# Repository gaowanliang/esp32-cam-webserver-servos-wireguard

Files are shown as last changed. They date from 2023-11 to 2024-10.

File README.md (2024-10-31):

# ESP32-CAM example revisited - Supports dual-degree-of-freedom servos and wireguard-based intranet penetration &nbsp;&nbsp;&nbsp; 
<span title="Master branch build status">

</span> &nbsp;&nbsp;
<span title="ESP EYE">ESP-EYE logo</span>

## Taken from the ESP examples, and expanded
> [!IMPORTANT]
> Since this code is old, it does not support esp32 version 3.x. Please use esp32 version 2.0.17 to compile it.
> 由于此代码较为老旧，所以不支持 esp32 3.x 版本，请使用esp32 2.0.17 版本编译

支持双自由度舵机和基于Wireuard的内网穿透

### Intranet Penetration Modifications

Configure your own wireguard parameters in myconfig.h

```c
// WireGuard settings
IPAddress local_ip(10, 0, 0, 2);                                            // IP address of the local interface
const char private_key[] = "oKXeV7gGtYTVcdgNKciDTkTLvmlZLbrzEcwpbXUDZH8=";  // Private key of the local interface
const char endpoint_address[] = "1.1.1.1";                           // Address of the endpoint peer
const char public_key[] = "0UWkW7oYVivNxoUX6OZWvhlpXcOeiX1FK682xNNDPxA=";   // Public key of the endpoint peer
uint16_t endpoint_port = 51280;                                             // Port of the endpoint peer
```

Your server can refer to the following configuration

```ini
[Interface]
Address = 10.0.0.1/24
ListenPort = 51280
PrivateKey = 8OZckuFQTgTczXnE0nJosrqVkxdi/GKS2fwmYOK53WA=

[Peer]
PublicKey = zV4LrlkKV7ne4zruqTgWfg6U4v7qL89YT2Q3I+5E7Gw=
AllowedIPs = 10.0.0.2/32
```
Please note, please do not use the above parameters directly, direct use may bring a series of security problems, you can use [this page](https://wg.orz.tools/) to generate your own `public key` and `private key`.

#### Refer

https://github.com/andr13/ESP32-Web-WireGuard

https://github.com/askew-etc/esp32-cam-webserver-servos

### Servo Modifications

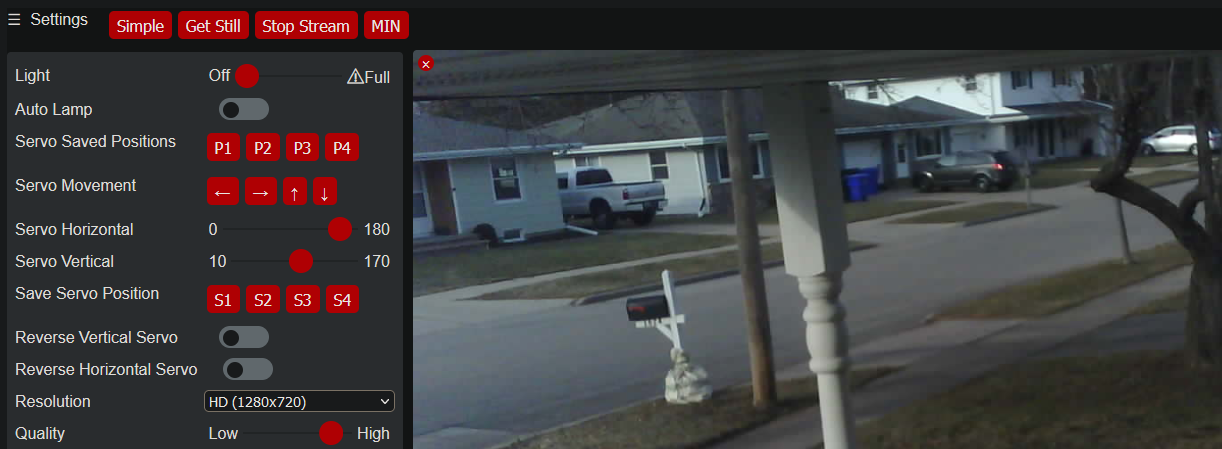
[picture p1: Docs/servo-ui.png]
Servo UI Screenshot


> [!NOTE]
> I'm in the process of redesigning this case, the current one may be too compact, while there are safety issues with not reserving a place for the charging port to be secured.

3D Printer files for tilt and pan with covers: https://www.thingiverse.com/thing:4621865.
You can buy the tilt and pan hardware with the screws along with the two servos from places like [Amazon](https://www.amazon.com/dp/B0775R6JFF) or [AliExpress](https://www.aliexpress.us/item/3256804363840656.html). Then you just need to 3D print Front_Cover.stl, Bottom_Cover.stl, and Mount_Original.stl.
I did exactly that, however the clips didn't quite catch on the two rectangular insets on the sides of Mount_Original.stl, so I used Blender to make them slightly bigger so that the clip could actually catch in them. Probably don't need to do that if printing all the pieces yourself since I assume they would just fit correcty. I've included these three files, two of which I modified to fit better. The front cover I modified as well since it fits a tad too tight with the back cover.
The pan and tilt [hardware](https://www.aliexpress.us/item/3256804363840656.html) and [servos](https://www.amazon.com/dp/B07Q6JGWNV) can be bought separately, useful if doing a bunch, or just utilizing one servo for panning only.

The servos use GPIO pins 12 and 13, making it easy to just use a four-pin female header to plug into the ESP-32, and then create the connections for input ground and power as well as the ground, power, and data lines of the servos.

In many applications the tilting feature is probably unnecessary and can be omitted to cut down on hardware.

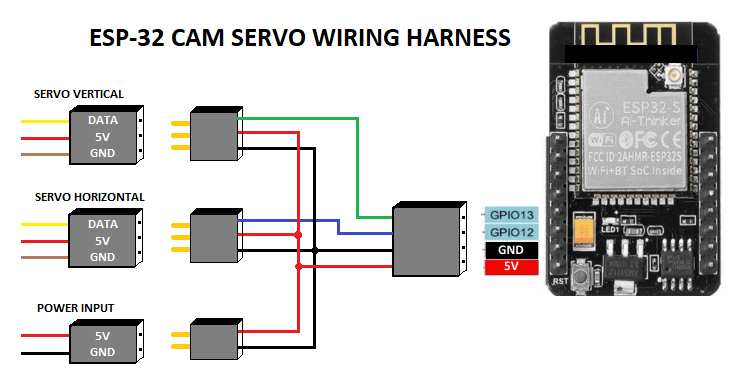
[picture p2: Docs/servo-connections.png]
Servo Wiring Harness


### Original Documentation

This sketch is a extension/expansion/rework of the 'official' ESP32 Camera example sketch from Espressif:

https://github.com/espressif/arduino-esp32/tree/master/libraries/ESP32/examples/Camera/CameraWebServer

But expanded with:
* Servo control (horizontal and vertical)
* More options for default network and camera settings
* Save and restore settings
* Control of on-board lamps, rotate the view in the browser
* Dedicated standalone stream viewer
* Over The Air firmware updates
* Lots of minor fixes and tweaks, documentation etc.

And 'reduced' by removing the Face Recognition features
* **If you want to try the Face Recognition features** please use the [`3.x` maintenance branch](https://github.com/easytarget/esp32-cam-webserver/tree/3.x), which still recieves bugfixes, but is not receiving any further development.
* They were a demo, only worked in low resolution modes, did not preserve the face database between power cycles, and were of little use in real-world applications.
* There are other (specialised) sketches for the ESP-CAM that do use face recognitioni more effectively, if this is your thing :-)

The original example is a bit incomprehensible and hard to modify as supplied. It is very focused on showing off the face recognition capabilities, and forgets the 'webcam' part.
* There are many other variants of a webcam server for these modules online, but most are created for a specific scenario and not good for general, casual, webcam use.

Actually, there are two cats in this image!

Hopefully this expanded example is more useful for those users who wish to set up a simple ESP32 based webcam using the cheap(ish) modules freely available online. Especially the AI-THINKER board:

#### AI-THINKER ESP32-CAM vs Other Modules:

I have four [AI-THINKER ESP32-CAM](https://github.com/raphaelbs/esp32-cam-ai-thinker/blob/master/assets/ESP32-CAM_Product_Specification.pdf) boards, so the descriptions below are for that board. But I took care to leave the default definitions and controls for other boards in the example intact. You may need to adjust the programming method to suit the your board, look for examples online.

* For some other good examples and information on ESP32 based webcams I also recommend the sketches here:
https://github.com/raphaelbs/esp32-cam-ai-thinker
* The AI thinker wiki can be quite informative, when run through an online translator and read sensibly:
https://wiki.ai-thinker.com/esp32-cam
* Default pinouts are also included for WRover Kit, ESP Eye and M5Stack esp32 camera modules.
  I do not have any of these boards, so they are untested by me. Please [let me know](https://github.com/easytarget/esp32-cam-webserver/issues) if you find issues or have a board not [in the list](./camera_pins.h).

## Troubleshooting:

A lot of common issues with this sketch are discussed and covered in the discussion forums:

https://github.com/easytarget/esp32-cam-webserver/discussions/categories/common-issues

The existing [issues list](https://github.com/easytarget/esp32-cam-webserver/issues?q=is%3Aissue) on Github is a good place to start if you have a specific issue not covered above or in the forums.

There is also this excellent guide for help with some common issues seen with the camera modules:
https://randomnerdtutorials.com/esp32-cam-troubleshooting-guide/

### Known Issues

Builds made with PlatformIO are currently (v4.0) broken; the stream will die shortly after starting. See https://github.com/easytarget/esp32-cam-webserver/issues/218 for more info.

The ESP32 itself is susceptible to the usual list of WiFi problems, not helped by having small antennas, older designs, congested airwaves and demanding users. The majority of disconnects, stutters and other comms problems are simply due to 'WiFi issues'. The AI-THINKER camera module & esp32 combination is quite susceptible to power supply problems affecting both WiFi conctivity and Video quality; short cabling and decent power supplies are your friend here; also well cooled cases and, if you have the time, decoupling capacitors on the power lines.

A basic limitation of the sketch is that it can can only support one stream at a time. If you try to connect to a cam that is already streaming (or attempting to stream) you will get no response and, eventually, a timeout. The stream itself is a [MJPEG stream](https://en.wikipedia.org/wiki/Motion_JPEG), which relies on the client (the web browser) to hold the connection open and request each new frame in turn via javascript. This can cause errors when browsers run into Javascript or caching problem, fail to request new frames or refuse to close the connection.
* If you cannot start the stream you can check the `/dump` page of the cam to see if it currently reports the camera as streaming or not.

Note that I do not respond to any Private Messages (via github, hackaday, or wherever) for support.

## Setup:

* For programming you will need a suitable development environment, I use the Arduino IDE, but this code should work in the Espressif development environment too.
* Make sure you are using the [latest version](https://www.arduino.cc/en/main/software#download) of the IDE and then follow [This Guide](https://docs.espressif.com/projects/arduino-esp32/en/latest/installing.html) to set up the Espressif Arduino core for the IDE.
* _I do not recommend or support running with development builds of either the IDE or the ESP arduino core._
* If you have a development board (anything that can be programmed via a standard USB cable/jack on the board itself) you are in luck. Just plug it in and skip ahead to the [config](#config) section. Remember to set your board model.
* The AI-THINKER board requires use of an external **3.3v** serial adapter to program; I use a `FTDI Friend` adapter, for more about this read AdaFruits excellent [FTDI Friend guide](https://learn.adafruit.com/ftdi-friend).
* Be careful not to use a 5v serial adapter since this will damage the ESP32.

### Wiring for AI-THINKER Boards (and similar clone-alikes)

Is pretty simple, You just need jumper wires, no soldering really required, see the diagram below.
Hoockup
* Connect the **RX** line from the serial adapter to the **TX** pin on ESP32
* The adapters **TX** line goes to the ESP32 **RX** pin
* The **GPIO0** pin of the ESP32 must be held LOW (to ground) when the unit is powered up to allow it to enter it's programming mode. This can be done with simple jumper cable connected at poweron, fitting a switch for this is useful if you will be reprogramming a lot.
* You must supply 5v to the ESP32 in order to power it during programming, the FTDI board can supply this.

### Download the Sketch, Unpack and Rename
Download the latest release of the sketch from https://github.com/easytarget/esp32-cam-webserver/releases/latest
- You can get the latest stable development release by cloning / downloading the `master` branch of the repo.

This will give you an archive file with the Version number in it, eg.`esp32-cam-webserver-4.0.zip`. You need to unpack this into your Arduino sketch folder, and then you need to **rename the folder you extracted to remove the version number**, eg.`esp32-cam-webserver-4.0` becomes `esp32-cam-webserver`.

Once you have done that you can open the sketch in the IDE by going to the `esp32-cam-webserver` sketch folder and selecting `esp32-cam-webserver.ino`.

### Config

By default the sketch assumes you have an AI-THINKER board, it creates an AccessPoint called `ESP32-CAM-CONNECT` and with the password `InsecurePassword`; connect to that and then browse to [`http://192.168.4.1/`](http://192.168.4.1/). This is nice and easy for testing and demo purposes.

To make a permanent config with your home wifi settings, different defaults or a different board; copy (or rename) the file `myconfig.sample.h` in the sketch folder to `myconfig.h` and edit that, all the usable defaults are in that file. Because this is your private copy of the config it will not get overwritten if you update the main sketch!

### Programming

Assuming you are using the latest Espressif Arduino core the `ESP32 Dev Module` board will appear in the ESP32 Arduino section of the boards list. Select this (do not use the `AI-THINKER` entry listed in the boiards menu, it is not OTA compatible, and will caus the module to crash and reboot rather than updating if you use it.
IDE board config

Make sure you select the `Minimal SPIFFS (1.9MB APP with OTA/190KB SPIFFS)` partition scheme and turn `PSRAM` on.

The first time you program (or if OTA is failing) you need to compile and upload the code from the IDE, and when the `Connecting...` appears in the console reboot the ESP32 module while keeping **GPIO0** grounded. You can release GPO0 once the sketch is uploading, most boards have a 'boot' button to trigger a reboot.

Once the upload completes (be patient, it can be a bit slow) open the serial monitor in the IDE and reboot the board again without GPIO0 grounded. In the serial monitor you should see the board start, connect to the wifi and then report the IP address it has been assigned.

Once you have the initial upload done and the board is connected to the wifi network you should see it appearing in the `network ports` list of the IDE, and you can upload wirelessly.

If you have a status LED configured it will give a double flash when it begins attempting to conenct to WiFi, and five short flashes once it has succeeded. It will also flash briefly when you access the camera to change settings.

Go to the URL given in the serial output, the web UI should appear with the settings panel open. Click away!

## My Modifications:

The simplified viewer<br>*The new default Simple view, just the basics*

The WiFi details can be stored in an (optional) header file to allow easier code development, and a camera name for the UI title can be configured. The lamp and status LED's are optional, and the lamp uses a exponential scale for brightness so that the control has some finess.

All of the face recognition code has been removed as of V4.0; this reduces the code size enough to allow OTA programming while improving compile and programming times.

The compressed and binary encoded HTML used in the example has been unpacked to raw text, this makes it much easier to access and modify the Javascript and UI elements. Given the relatively small size of the index page there is very little benefit from compressing it.

The streamviewer, lamp control, and all the other new features have been added. I have tried to retain the basic structure of the original example,extending where necessary.

The web UI has had changes to add the lamp control (only when enabled) and make the streamm window rotate and resize appropriately. I also made the 'Start Stream' and 'Snapshot' controls more prominent, and added feedback of the camera name + firmware.

I would also like to shoutout to @jmfloyd; who suggested rotating the image in the browser since the esp32 itself cannot do this.

The stream viewer<br>*Standalone StreamViewer; No decoration or controls, the image is resizable, and you can doubleclick it for fullscreen*

The info page<br>*Boring Details, useful when debugging or if you want to check stats*

### API
The communications between the web browser and the camera module can also be used to send commands directly to the camera (eg to automate it, etc) and form, in effect, an API for the camera.
* I have [documented this here](https://github.com/easytarget/esp32-cam-webserver/blob/master/API.md).

## Notes:

* I only have AI-THINKER modules with OV2640 camera installed; so I have only been able to test with this combination. I have attempted to preserve all the code for other boards and the OV3660 module, and I have merged all changes for the WebUI etc, but I cannot guarantee operation for these.
* I created a small board with a handy switch for power, a pushbutton for the GPIO0 programming switch, and a socket for the AI-THINKER board. This proved very useful for development work and programming multiple devices.
* I found some excellent [cases on Thingieverse](https://www.thingiverse.com/thing:3708345).

Cameras and a Programmer

## Contributing

Contributions are welcome; please see the [Contribution guidelines](CONTRIBUTING.md).

## Plans

Time allowing; my Current plan is:

V4
* Investigate using SD card to capture images
* Implement a better network stack for remembering multiple AP's, auto-config etc.
  * Advanced (web upload) OTA might be nice to have if possible
* UI Skinning/Theming
* OSD
  * Temperature/humidity/pressure sensor support (bme20,dht11)
You can check the [enhancement list](https://github.com/easytarget/esp32-cam-webserver/issues?q=is%3Aissue+label%3Aenhancement) (past and present), and add any thoughts you may have there.

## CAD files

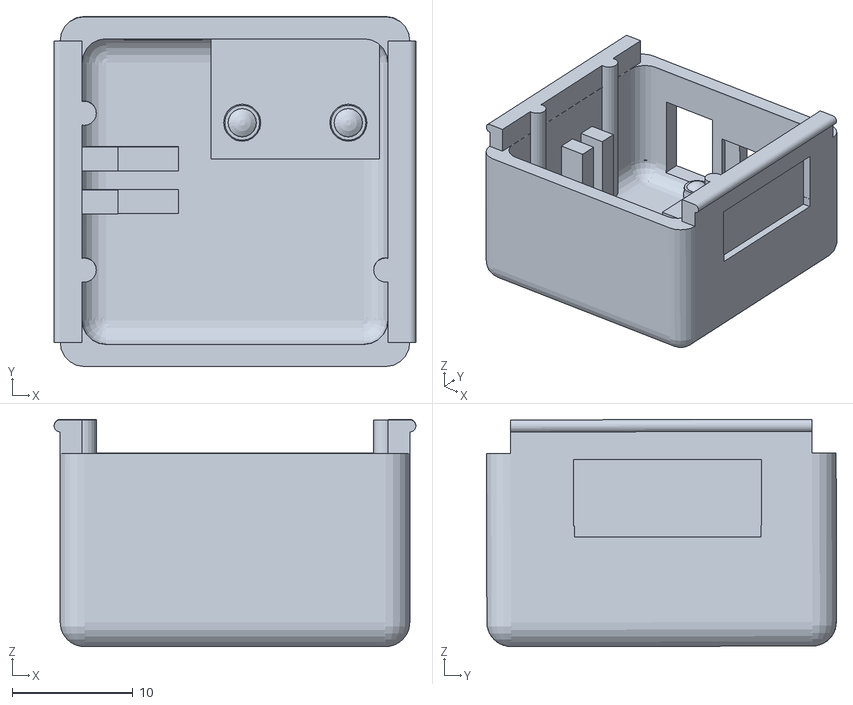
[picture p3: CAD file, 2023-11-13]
3DPrintFiles/Mount_Original_modified.stl
30.0 x 29.0 x 18.8

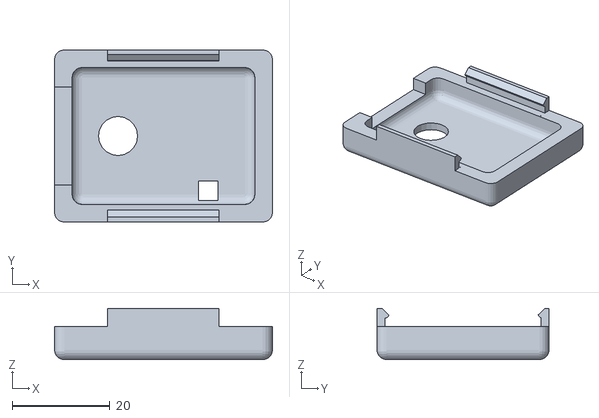
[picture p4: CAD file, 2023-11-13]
3DPrintFiles/Front_Cover_modified.stl
44.6 x 35.2 x 10.4

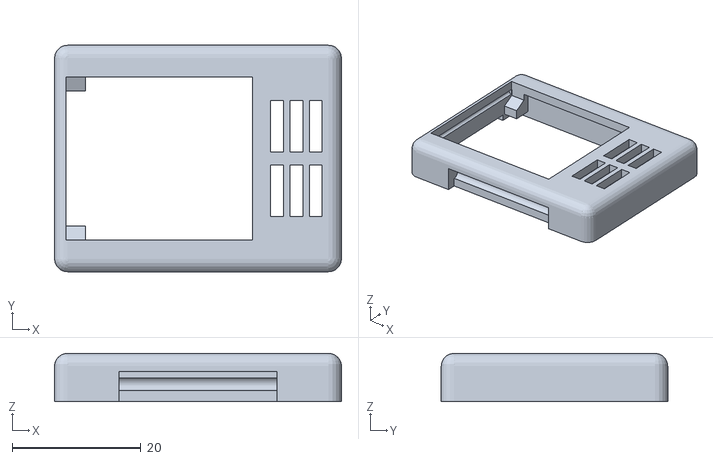
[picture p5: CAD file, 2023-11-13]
3DPrintFiles/Bottom_Cover.stl
44.6 x 35.2 x 7.50

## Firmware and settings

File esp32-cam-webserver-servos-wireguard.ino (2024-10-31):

#include <esp_camera.h>
#include <esp_int_wdt.h>
#include <esp_task_wdt.h>
#include <WiFi.h>
#include <DNSServer.h>
#include <WiFiUdp.h>
#include <ArduinoOTA.h>
#include "src/parsebytes.h"
#include "time.h"
#include <ESPmDNS.h>
//#include <ESP32Servo.h>
#include "soc/soc.h"           // disable brownout problems
#include "soc/rtc_cntl_reg.h"  // disable brownout problems
#include "src/WireGuard-ESP32.h"


// WireGuard class instance
static WireGuard wg;

/* This sketch is a extension/expansion/reork of the 'official' ESP32 Camera example
 *  sketch from Expressif:
 *  https://github.com/espressif/arduino-esp32/tree/master/libraries/ESP32/examples/Camera/CameraWebServer
 *
 *  It is modified to allow control of Illumination LED Lamps's (present on some modules),
 *  greater feedback via a status LED, and the HTML contents are present in plain text
 *  for easy modification.
 *
 *  A camera name can now be configured, and wifi details can be stored in an optional
 *  header file to allow easier updated of the repo.
 *
 *  The web UI has had changes to add the lamp control, rotation, a standalone viewer,
 *  more feeedback, new controls and other tweaks and changes,
 * note: Make sure that you have either selected ESP32 AI Thinker,
 *       or another board which has PSRAM enabled to use high resolution camera modes
 */


/*
 *  FOR NETWORK AND HARDWARE SETTINGS COPY OR RENAME 'myconfig.sample.h' TO 'myconfig.h' AND EDIT THAT.
 *
 * By default this sketch will assume an AI-THINKER ESP-CAM and create
 * an accesspoint called "ESP32-CAM-CONNECT" (password: "InsecurePassword")
 *
 */

// Primary config, or defaults.
#if __has_include("myconfig.h")
struct station {
  const char ssid[65];
  const char password[65];
  const bool dhcp;
};  // do no edit
#include "myconfig.h"
#else
#warning "Using Defaults: Copy myconfig.sample.h to myconfig.h and edit that to use your own settings"
#define WIFI_AP_ENABLE
#define CAMERA_MODEL_AI_THINKER
struct station {
  const char ssid[65];
  const char password[65];
  const bool dhcp;
} stationList[] = { { "ESP32-CAM-CONNECT", "InsecurePassword", true } };
#endif

// Upstream version string
#include "src/version.h"

// Pin Mappings
#include "camera_pins.h"

// Camera config structure
camera_config_t config;

// Internal filesystem (SPIFFS)
// used for non-volatile camera settings
#include "storage.h"

// Sketch Info
int sketchSize;
int sketchSpace;
String sketchMD5;

// Start with accesspoint mode disabled, wifi setup will activate it if
// no known networks are found, and WIFI_AP_ENABLE has been defined
bool accesspoint = false;

// IP address, Netmask and Gateway, populated when connected
IPAddress ip;
IPAddress net;
IPAddress gw;

// Declare external function from app_httpd.cpp
extern void startCameraServer(int hPort, int sPort);
extern void serialDump();

// Names for the Camera. (set these in myconfig.h)
#if defined(CAM_NAME)
char myName[] = CAM_NAME;
#else
char myName[] = "ESP32 camera server";
#endif

#if defined(MDNS_NAME)
char mdnsName[] = MDNS_NAME;
#else
char mdnsName[] = "esp32-cam";
#endif

// Ports for http and stream (override in myconfig.h)
#if defined(HTTP_PORT)
int httpPort = HTTP_PORT;
#else
int httpPort = 80;
#endif

#if defined(STREAM_PORT)
int streamPort = STREAM_PORT;
#else
int streamPort = 81;
#endif

#if !defined(WIFI_WATCHDOG)
#define WIFI_WATCHDOG 15000
#endif

// Number of known networks in stationList[]
int stationCount = sizeof(stationList) / sizeof(stationList[0]);

// If we have AP mode enabled, ignore first entry in the stationList[]
#if defined(WIFI_AP_ENABLE)
int firstStation = 1;
#else
int firstStation = 0;
#endif

// Select between full and simple index as the default.
#if defined(DEFAULT_INDEX_FULL)
char default_index[] = "full";
#else
char default_index[] = "simple";
#endif

// DNS server
const byte DNS_PORT = 53;
DNSServer dnsServer;
bool captivePortal = false;
char apName[64] = "Undefined";

// The app and stream URLs
char httpURL[64] = { "Undefined" };
char streamURL[64] = { "Undefined" };

// Counters for info screens and debug
int8_t streamCount = 0;           // Number of currently active streams
unsigned long streamsServed = 0;  // Total completed streams
unsigned long imagesServed = 0;   // Total image requests

// This will be displayed to identify the firmware
char myVer[] PROGMEM = __DATE__ " @ " __TIME__;

// This will be set to the sensors PID (identifier) during initialisation
//camera_pid_t sensorPID;
int sensorPID;

// Camera module bus communications frequency.
// Originally: config.xclk_freq_mhz = 20000000, but this lead to visual artifacts on many modules.
// See https://github.com/espressif/esp32-camera/issues/150#issuecomment-726473652 et al.
#if !defined(XCLK_FREQ_MHZ)
unsigned long xclk = 8;
#else
unsigned long xclk = XCLK_FREQ_MHZ;
#endif

// initial rotation
// can be set in myconfig.h
#if !defined(CAM_ROTATION)
#define CAM_ROTATION 0
#endif
int myRotation = CAM_ROTATION;

// minimal frame duration in ms, effectively 1/maxFPS
#if !defined(MIN_FRAME_TIME)
#define MIN_FRAME_TIME 0
#endif
int minFrameTime = MIN_FRAME_TIME;

// Illumination LAMP and status LED
#if defined(LAMP_DISABLE)
int lampVal = -1;  // lamp is disabled in config
#elif defined(LAMP_PIN)
#if defined(LAMP_DEFAULT)
int lampVal = constrain(LAMP_DEFAULT, 0, 100);  // initial lamp value, range 0-100
#else
int lampVal = 0;  //default to off
#endif
#else
int lampVal = -1;  // no lamp pin assigned
#endif

#if defined(LED_DISABLE)
#undef LED_PIN  // undefining this disables the notification LED
#endif

bool autoLamp = false;  // Automatic lamp (auto on while camera running)

int lampChannel = 7;          // a free PWM channel (some channels used by camera)
const int pwmfreq = 50000;    // 50K pwm frequency
const int pwmresolution = 9;  // duty cycle bit range
const int pwmMax = pow(2, pwmresolution) - 1;

#if defined(NO_FS)
bool filesystem = false;
#else
bool filesystem = true;
#endif

#if defined(NO_OTA)
bool otaEnabled = false;
#else
bool otaEnabled = true;
#endif

#if defined(OTA_PASSWORD)
char otaPassword[] = OTA_PASSWORD;
#else
char otaPassword[] = "";
#endif

#if defined(NTPSERVER)
bool haveTime = true;
const char* ntpServer = NTPSERVER;
const long gmtOffset_sec = NTP_GMT_OFFSET;
const int daylightOffset_sec = NTP_DST_OFFSET;
#else
bool haveTime = false;
const char* ntpServer = "";
const long gmtOffset_sec = 0;
const int daylightOffset_sec = 0;
#endif

// Critical error string; if set during init (camera hardware failure) it
// will be returned for all http requests
String critERR = "";

// Debug flag for stream and capture data
bool debugData;

// servo vars
const int servoMoveAmt = 10;
int servoVert = 90;
int servoHorz = 90;
//#define DUMMY_SERVO_1 14
//#define DUMMY_SERVO_2 15
#define SERVO_1 12
#define SERVO_2 13
#define SERVO_STEP 5
#define SERVO_VERT_CH 2  // channels for servos
#define SERVO_HORZ_CH 4
//Servo servoN1;
//Servo servoN2;
//Servo servo1;
//Servo servo2;
bool reverseVert = false;
bool reverseHorz = false;
char servoPos1[8] = "100-100";
char servoPos2[8] = "100-100";
char servoPos3[8] = "100-100";
char servoPos4[8] = "100-100";

void debugOn() {
  debugData = true;
  Serial.println("Camera debug data is enabled (send 'd' for status dump, or any other char to disable debug)");
}

void debugOff() {
  debugData = false;
  Serial.println("Camera debug data is disabled (send 'd' for status dump, or any other char to enable debug)");
}

// Serial input (debugging controls)
void handleSerial() {
  if (Serial.available()) {
    char cmd = Serial.read();
    if (cmd == 'd') {
      serialDump();
    } else {
      if (debugData) debugOff();
      else debugOn();
    }
  }
  while (Serial.available()) Serial.read();  // chomp the buffer
}

// Notification LED
void flashLED(int flashtime) {
#if defined(LED_PIN)               // If we have it; flash it.
  digitalWrite(LED_PIN, LED_ON);   // On at full power.
  delay(flashtime);                // delay
  digitalWrite(LED_PIN, LED_OFF);  // turn Off
#else
  return;  // No notifcation LED, do nothing, no delay
#endif
}

// Lamp Control
void setLamp(int newVal) {
#if defined(LAMP_PIN)
  if (newVal != -1) {
    // Apply a logarithmic function to the scale.
    int brightness = round((pow(2, (1 + (newVal * 0.02))) - 2) / 6 * pwmMax);
    ledcWrite(lampChannel, brightness);
    Serial.print("Lamp: ");
    Serial.print(newVal);
    Serial.print("%, pwm = ");
    Serial.println(brightness);
  }
#endif
}

// Arduino like analogWrite
// value has to be between 0 and valueMax
// (used for servos)
void ledcAnalogWrite(uint8_t channel, uint32_t value, uint32_t valueMax = 180) {
  // calculate duty, 8191 from 2 ^ 13 - 1
  uint32_t duty = (8191 / valueMax) * min(value, valueMax);
  ledcWrite(channel, duty);
}

void moveServoVert() {
  //servo1.write(servoVert);
  //ledcAnalogWrite(2, servoVert); // channel, 0-180
  ledcAnalogWrite(SERVO_VERT_CH, servoVert);  // channel, 0-180
  //Serial.print("Servo Vert: ");
  //Serial.println(servoVert);
}

void moveServoHorz() {
  //servo2.write(servoHorz);
  //ledcAnalogWrite(4, servoHorz); // channel, 0-180)
  ledcAnalogWrite(SERVO_HORZ_CH, servoHorz);  // channel, 0-180
  //Serial.print("Servo Horz: ");
  //Serial.println(servoHorz);
}

void printLocalTime(bool extraData = false) {
  struct tm timeinfo;
  if (!getLocalTime(&timeinfo)) {
    Serial.println("Failed to obtain time");
  } else {
    Serial.println(&timeinfo, "%H:%M:%S, %A, %B %d %Y");
  }
  if (extraData) {
    Serial.printf("NTP Server: %s, GMT Offset: %li(s), DST Offset: %i(s)\r\n", ntpServer, gmtOffset_sec, daylightOffset_sec);
  }
}

void calcURLs() {
// Set the URL's
#if defined(URL_HOSTNAME)
  if (httpPort != 80) {
    sprintf(httpURL, "http://%s:%d/", URL_HOSTNAME, httpPort);
  } else {
    sprintf(httpURL, "http://%s/", URL_HOSTNAME);
  }
  sprintf(streamURL, "http://%s:%d/", URL_HOSTNAME, streamPort);
#else
  Serial.println("Setting httpURL");
  if (httpPort != 80) {
    sprintf(httpURL, "http://%d.%d.%d.%d:%d/", ip[0], ip[1], ip[2], ip[3], httpPort);
  } else {
    sprintf(httpURL, "http://%d.%d.%d.%d/", ip[0], ip[1], ip[2], ip[3]);
  }
  sprintf(streamURL, "http://%d.%d.%d.%d:%d/", ip[0], ip[1], ip[2], ip[3], streamPort);
#endif
}

void StartCamera() {
  // Populate camera config structure with hardware and other defaults
  config.ledc_channel = LEDC_CHANNEL_0;
  config.ledc_timer = LEDC_TIMER_0;
  config.pin_d0 = Y2_GPIO_NUM;
  config.pin_d1 = Y3_GPIO_NUM;
  config.pin_d2 = Y4_GPIO_NUM;
  config.pin_d3 = Y5_GPIO_NUM;
  config.pin_d4 = Y6_GPIO_NUM;
  config.pin_d5 = Y7_GPIO_NUM;
  config.pin_d6 = Y8_GPIO_NUM;
  config.pin_d7 = Y9_GPIO_NUM;
  config.pin_xclk = XCLK_GPIO_NUM;
  config.pin_pclk = PCLK_GPIO_NUM;
  config.pin_vsync = VSYNC_GPIO_NUM;
  config.pin_href = HREF_GPIO_NUM;
  config.pin_sscb_sda = SIOD_GPIO_NUM;
  config.pin_sscb_scl = SIOC_GPIO_NUM;
  config.pin_pwdn = PWDN_GPIO_NUM;
  config.pin_reset = RESET_GPIO_NUM;
  config.xclk_freq_hz = xclk * 1000000;
  config.pixel_format = PIXFORMAT_JPEG;
  // Low(ish) default framesize and quality
  config.frame_size = FRAMESIZE_SVGA;
  config.jpeg_quality = 12;
  config.fb_location = CAMERA_FB_IN_PSRAM;
  config.fb_count = 2;
  config.grab_mode = CAMERA_GRAB_LATEST;

#if defined(CAMERA_MODEL_ESP_EYE)
  pinMode(13, INPUT_PULLUP);
  pinMode(14, INPUT_PULLUP);
#endif

  // camera init
  esp_err_t err = esp_camera_init(&config);
  if (err != ESP_OK) {
    delay(100);  // need a delay here or the next serial o/p gets missed
    Serial.printf("\r\n\r\nCRITICAL FAILURE: Camera sensor failed to initialise.\r\n\r\n");
    Serial.printf("A full (hard, power off/on) reboot will probably be needed to recover from this.\r\n");
    Serial.printf("Meanwhile; this unit will reboot in 1 minute since these errors sometime clear automatically\r\n");
    // Reset the I2C bus.. may help when rebooting.
    periph_module_disable(PERIPH_I2C0_MODULE);  // try to shut I2C down properly in case that is the problem
    periph_module_disable(PERIPH_I2C1_MODULE);
    periph_module_reset(PERIPH_I2C0_MODULE);
    periph_module_reset(PERIPH_I2C1_MODULE);
    // And set the error text for the UI
    critERR = "<h1>Error!</h1><hr><p>Camera module failed to initialise!</p><p>Please reset (power off/on) the camera.</p>";
    critERR += "<p>We will continue to reboot once per minute since this error sometimes clears automatically.</p>";
    // Start a 60 second watchdog timer
    esp_task_wdt_init(60, true);
    esp_task_wdt_add(NULL);
  } else {
    Serial.println("Camera init succeeded");

    // Get a reference to the sensor
    sensor_t* s = esp_camera_sensor_get();

    // Dump camera module, warn for unsupported modules.
    sensorPID = s->id.PID;
    switch (sensorPID) {
      case OV9650_PID: Serial.println("WARNING: OV9650 camera module is not properly supported, will fallback to OV2640 operation"); break;
      case OV7725_PID: Serial.println("WARNING: OV7725 camera module is not properly supported, will fallback to OV2640 operation"); break;
      case OV2640_PID: Serial.println("OV2640 camera module detected"); break;
      case OV3660_PID: Serial.println("OV3660 camera module detected"); break;
      default: Serial.println("WARNING: Camera module is unknown and not properly supported, will fallback to OV2640 operation");
    }

    // OV3660 initial sensors are flipped vertically and colors are a bit saturated
    if (sensorPID == OV3660_PID) {
      s->set_vflip(s, 1);        //flip it back
      s->set_brightness(s, 1);   //up the blightness just a bit
      s->set_saturation(s, -2);  //lower the saturation
    }

// M5 Stack Wide has special needs
#if defined(CAMERA_MODEL_M5STACK_WIDE)
    s->set_vflip(s, 1);
    s->set_hmirror(s, 1);
#endif

// Config can override mirror and flip
#if defined(H_MIRROR)
    s->set_hmirror(s, H_MIRROR);
#endif
#if defined(V_FLIP)
    s->set_vflip(s, V_FLIP);
#endif

// set initial frame rate
#if defined(DEFAULT_RESOLUTION)
    s->set_framesize(s, DEFAULT_RESOLUTION);
#endif

    /*
        * Add any other defaults you want to apply at startup here:
        * uncomment the line and set the value as desired (see the comments)
        *
        * these are defined in the esp headers here:
        * https://github.com/espressif/esp32-camera/blob/master/driver/include/sensor.h#L149
        */

    //s->set_framesize(s, FRAMESIZE_SVGA); // FRAMESIZE_[QQVGA|HQVGA|QVGA|CIF|VGA|SVGA|XGA|SXGA|UXGA|QXGA(ov3660)]);
    //s->set_quality(s, val);       // 10 to 63
    //s->set_brightness(s, 0);      // -2 to 2
    //s->set_contrast(s, 0);        // -2 to 2
    //s->set_saturation(s, 0);      // -2 to 2
    //s->set_special_effect(s, 0);  // 0 to 6 (0 - No Effect, 1 - Negative, 2 - Grayscale, 3 - Red Tint, 4 - Green Tint, 5 - Blue Tint, 6 - Sepia)
    //s->set_whitebal(s, 1);        // aka 'awb' in the UI; 0 = disable , 1 = enable
    //s->set_awb_gain(s, 1);        // 0 = disable , 1 = enable
    //s->set_wb_mode(s, 0);         // 0 to 4 - if awb_gain enabled (0 - Auto, 1 - Sunny, 2 - Cloudy, 3 - Office, 4 - Home)
    //s->set_exposure_ctrl(s, 1);   // 0 = disable , 1 = enable
    //s->set_aec2(s, 0);            // 0 = disable , 1 = enable
    //s->set_ae_level(s, 0);        // -2 to 2
    //s->set_aec_value(s, 300);     // 0 to 1200
    //s->set_gain_ctrl(s, 1);       // 0 = disable , 1 = enable
    //s->set_agc_gain(s, 0);        // 0 to 30
    //s->set_gainceiling(s, (gainceiling_t)0);  // 0 to 6
    //s->set_bpc(s, 0);             // 0 = disable , 1 = enable
    //s->set_wpc(s, 1);             // 0 = disable , 1 = enable
    //s->set_raw_gma(s, 1);         // 0 = disable , 1 = enable
    //s->set_lenc(s, 1);            // 0 = disable , 1 = enable
    //s->set_hmirror(s, 0);         // 0 = disable , 1 = enable
    //s->set_vflip(s, 0);           // 0 = disable , 1 = enable
    //s->set_dcw(s, 1);             // 0 = disable , 1 = enable
    //s->set_colorbar(s, 0);        // 0 = disable , 1 = enable
  }
  // We now have camera with default init
}
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
void loop() {
  /*
     *  Just loop forever, reconnecting Wifi As necesscary in client mode
     * The stream and URI handler processes initiated by the startCameraServer() call at the
     * end of setup() will handle the camera and UI processing from now on.
    */
  if (accesspoint) {
    // Accespoint is permanently up, so just loop, servicing the captive portal as needed
    // Rather than loop forever, follow the watchdog, in case we later add auto re-scan.
    unsigned long start = millis();
    while (millis() - start < WIFI_WATCHDOG) {
      delay(100);
      if (otaEnabled) ArduinoOTA.handle();
      handleSerial();
      if (captivePortal) dnsServer.processNextRequest();
    }
  } else {
    // client mode can fail; so reconnect as appropriate
    static bool warned = false;
    if (WiFi.status() == WL_CONNECTED) {
      // We are connected, wait a bit and re-check
      if (warned) {
        // Tell the user if we have just reconnected
        Serial.println("WiFi reconnected");
        warned = false;
      }
      // loop here for WIFI_WATCHDOG, turning debugData true/false depending on serial input..
      unsigned long start = millis();
      while (millis() - start < WIFI_WATCHDOG) {
        delay(100);
        if (otaEnabled) ArduinoOTA.handle();
        handleSerial();
      }
    } else {
      // disconnected; attempt to reconnect
      if (!warned) {
        // Tell the user if we just disconnected
        WiFi.disconnect();  // ensures disconnect is complete, wifi scan cleared
        Serial.println("WiFi disconnected, retrying");
        warned = true;
      }
      WifiSetup();
    }
  }
}

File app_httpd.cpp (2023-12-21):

// Original Copyright 2015-2016 Espressif Systems (Shanghai) PTE LTD
//
// Licensed under the Apache License, Version 2.0 (the "License");
// you may not use this file except in compliance with the License.
// You may obtain a copy of the License at
//
//     http://www.apache.org/licenses/LICENSE-2.0
//
// Unless required by applicable law or agreed to in writing, software
// distributed under the License is distributed on an "AS IS" BASIS,
// WITHOUT WARRANTIES OR CONDITIONS OF ANY KIND, either express or implied.
// See the License for the specific language governing permissions and
// limitations under the License.

#include <esp_http_server.h>
#include <esp_timer.h>
#include <esp_camera.h>
#include <esp_int_wdt.h>
#include <esp_task_wdt.h>
#include <Arduino.h>
#include <WiFi.h>

#include "index_ov2640.h"
#include "index_ov3660.h"
#include "index_other.h"
#include "css.h"
#include "src/favicons.h"
#include "src/logo.h"
#include "storage.h"

// Functions from the main .ino
extern void flashLED(int flashtime);
extern void setLamp(int newVal);
extern void printLocalTime(bool extraData);
extern void moveServoVert();
extern void moveServoHorz();

// External variables declared in the main .ino
extern char myName[];
extern char myVer[];
extern char baseVersion[];
extern IPAddress ip;
extern IPAddress net;
extern IPAddress gw;
extern bool accesspoint;
extern char apName[];
extern bool captivePortal;
extern int httpPort;
extern int streamPort;
extern char httpURL[];
extern char streamURL[];
extern char default_index[];
extern int8_t streamCount;
extern unsigned long streamsServed;
extern unsigned long imagesServed;
extern int myRotation;
extern int minFrameTime;
extern int lampVal;
extern bool autoLamp;
extern bool filesystem;
extern String critERR;
extern bool debugData;
extern bool haveTime;
extern int sketchSize;
extern int sketchSpace;
extern String sketchMD5;
extern bool otaEnabled;
extern char otaPassword[];
extern unsigned long xclk;
extern int sensorPID;
extern int servoVert;
extern int servoHorz;
extern bool reverseVert;
extern bool reverseHorz;
extern char servoPos1[];
extern char servoPos2[];
extern char servoPos3[];
extern char servoPos4[];

typedef struct {
        httpd_req_t *req;
        size_t len;
} jpg_chunking_t;

#define PART_BOUNDARY "123456789000000000000987654321"
static const char* _STREAM_CONTENT_TYPE = "multipart/x-mixed-replace;boundary=" PART_BOUNDARY;
static const char* _STREAM_BOUNDARY = "\r\n--" PART_BOUNDARY "\r\n";
static const char* _STREAM_PART = "Content-Type: image/jpeg\r\nContent-Length: %u\r\n\r\n";

httpd_handle_t stream_httpd = NULL;
httpd_handle_t camera_httpd = NULL;

// Flag that can be set to kill all active streams
bool streamKill;

#ifdef __cplusplus
extern "C" {
#endif
uint8_t temprature_sens_read();
#ifdef __cplusplus
}
#endif

void serialDump() {
    Serial.println();
    // Module
    Serial.printf("Name: %s\r\n", myName);
    if (haveTime) {
        Serial.print("Time: ");
        printLocalTime(true);
    }
    Serial.printf("Firmware: %s (base: %s)\r\n", myVer, baseVersion);
    float sketchPct = 100 * sketchSize / sketchSpace;
    Serial.printf("Sketch Size: %i (total: %i, %.1f%% used)\r\n", sketchSize, sketchSpace, sketchPct);
    Serial.printf("MD5: %s\r\n", sketchMD5.c_str());
    Serial.printf("ESP sdk: %s\r\n", ESP.getSdkVersion());
    if (otaEnabled) {
         if (strlen(otaPassword) != 0) {
            Serial.printf("OTA: Enabled, Password: %s\n\r", otaPassword);
         } else {
            Serial.printf("OTA: Enabled, No Password! (insecure)\n\r");
         }
    } else {
        Serial.printf("OTA: Disabled\n\r");
    }
    // Network
    if (accesspoint) {
        if (captivePortal) {
            Serial.printf("WiFi Mode: AccessPoint with captive portal\r\n");
        } else {
            Serial.printf("WiFi Mode: AccessPoint\r\n");
        }
        Serial.printf("WiFi SSID: %s\r\n", apName);
    } else {
        Serial.printf("WiFi Mode: Client\r\n");
        String ssidName = WiFi.SSID();
        Serial.printf("WiFi Ssid: %s\r\n", ssidName.c_str());
        Serial.printf("WiFi Rssi: %i\r\n", WiFi.RSSI());
        String bssid = WiFi.BSSIDstr();
        Serial.printf("WiFi BSSID: %s\r\n", bssid.c_str());
    }
    Serial.printf("WiFi IP address: %d.%d.%d.%d\r\n", ip[0], ip[1], ip[2], ip[3]);
    if (!accesspoint) {
        Serial.printf("WiFi Netmask: %d.%d.%d.%d\r\n", net[0], net[1], net[2], net[3]);
        Serial.printf("WiFi Gateway: %d.%d.%d.%d\r\n", gw[0], gw[1], gw[2], gw[3]);
    }
    Serial.printf("WiFi Http port: %i, Stream port: %i\r\n", httpPort, streamPort);
    byte mac[6];
    WiFi.macAddress(mac);
    Serial.printf("WiFi MAC: %02X:%02X:%02X:%02X:%02X:%02X\r\n", mac[0], mac[1], mac[2], mac[3], mac[4], mac[5]);
    // System
    int64_t sec = esp_timer_get_time() / 1000000;
    int64_t upDays = int64_t(floor(sec/86400));
    int upHours = int64_t(floor(sec/3600)) % 24;
    int upMin = int64_t(floor(sec/60)) % 60;
    int upSec = sec % 60;
    int McuTc = (temprature_sens_read() - 32) / 1.8; // celsius
    int McuTf = temprature_sens_read(); // fahrenheit
    Serial.printf("System up: %" PRId64 ":%02i:%02i:%02i (d:h:m:s)\r\n", upDays, upHours, upMin, upSec);
    Serial.printf("Active streams: %i, Previous streams: %lu, Images captured: %lu\r\n", streamCount, streamsServed, imagesServed);
    Serial.printf("CPU Freq: %i MHz, Xclk Freq: %i MHz\r\n", ESP.getCpuFreqMHz(), xclk);
    Serial.printf("MCU temperature : %i C, %i F  (approximate)\r\n", McuTc, McuTf);
    Serial.printf("Heap: %i, free: %i, min free: %i, max block: %i\r\n", ESP.getHeapSize(), ESP.getFreeHeap(), ESP.getMinFreeHeap(), ESP.getMaxAllocHeap());
    if(psramFound()) {
        Serial.printf("Psram: %i, free: %i, min free: %i, max block: %i\r\n", ESP.getPsramSize(), ESP.getFreePsram(), ESP.getMinFreePsram(), ESP.getMaxAllocPsram());
    } else {
        Serial.printf("Psram: Not found; please check your board configuration.\r\n");
        Serial.printf("- High resolution/quality settings will show incomplete frames to low memory.\r\n");
    }
    // Filesystems
    if (filesystem && (SPIFFS.totalBytes() > 0)) {
        Serial.printf("Spiffs: %i, used: %i\r\n", SPIFFS.totalBytes(), SPIFFS.usedBytes());
    } else {
        Serial.printf("Spiffs: No filesystem found, please check your board configuration.\r\n");
        Serial.printf("- Saving and restoring camera settings will not function without this.\r\n");
    }
    Serial.println("Preferences file: ");
    dumpPrefs(SPIFFS);
    if (critERR.length() > 0) {
        Serial.printf("\r\n\r\nAn error or halt has occurred with Camera Hardware, see previous messages.\r\n");
        Serial.printf("A reboot is required to recover from this.\r\nError message: (html)\r\n %s\r\n\r\n", critERR.c_str());
    }
    Serial.println();
    return;
}
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

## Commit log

2023-11-12 Initial commit of all changes, working correctly.
    [app_httpd.cpp, css.h, storage.cpp]
2023-11-12 README updated with servo ui screenshot
2023-11-12 Cropped servo-ui.png
2023-11-12 Updated docs with servo wiring harness
2023-11-12 updated servo connections pic
2023-11-12 Switched servo horz/vert slider positions in UI
2023-11-13 3D print files added, readme changed to reflect change.
    [Bottom_Cover.stl, Front_Cover_modified.stl, Mount_Original_modified.stl]
2023-11-13 Added button to show important controls only so using servos on mobile is easier
2023-12-21 Servo save positions added
